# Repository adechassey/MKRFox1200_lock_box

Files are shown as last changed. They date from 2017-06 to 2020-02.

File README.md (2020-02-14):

# [MKRFox1200](http://www.sigfox.com/) Lock Box :key: 

<a href="https://www.buymeacoffee.com/antoine" target="_blank">Buy Me A Coffee</a>

What if you had to store something precious to be picked up by someone you do not know?
What if you were far away from the box and had to change the password for security reasons?

This is where Sigfox comes in! Indeed, Sigfox allows you to use 4 downlink messages per day. The idea is to be able to __update the password controlling the opening of the box__. Therefore in this tutorial, every 6 hours (4 times per day), the box's password will be set with a newly generated one from a web application. The owner can then decide to share the password to whom he wants. He will also __be notified every time the box is opened__!

<p align="center">
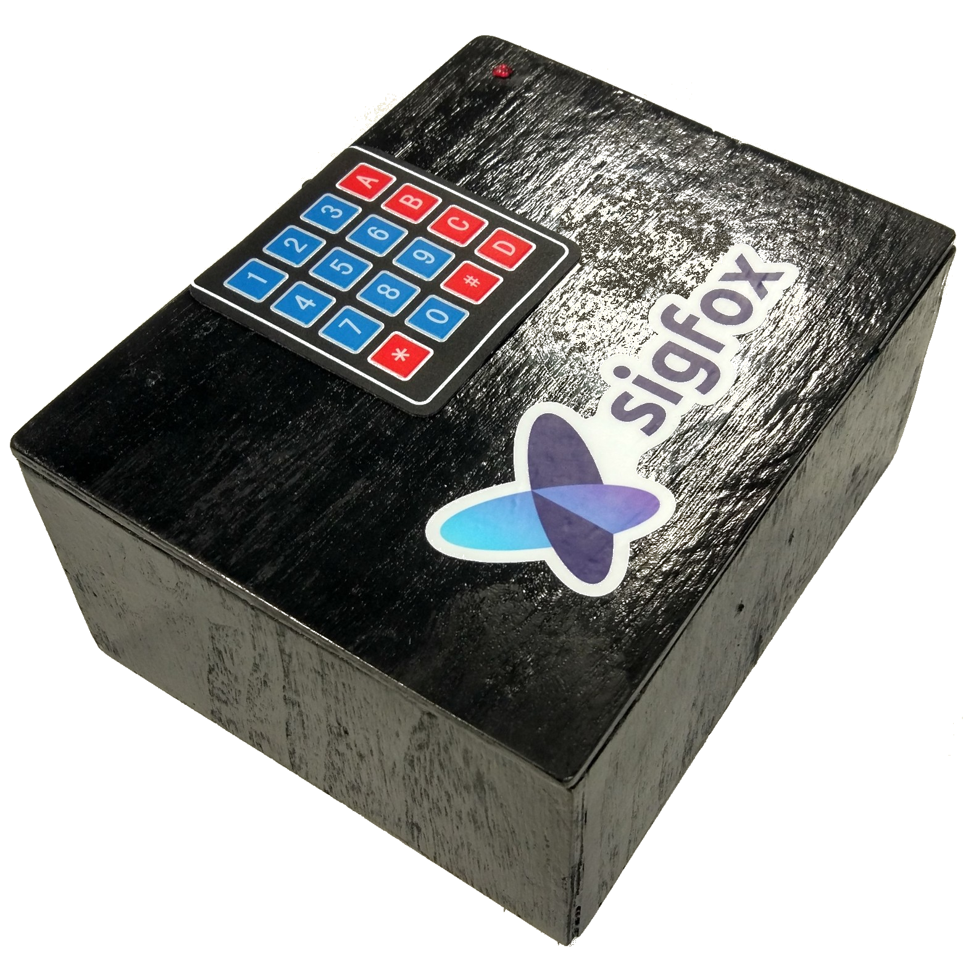
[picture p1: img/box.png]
    
</p>

This repository includes:
- the firmware to upload on the MKRFox1200
- the web API generating a new password and receiving the box's notifications

A video presentation is available [here](https://youtu.be/BI61gZuiOqs)!

Some photos showing how the mechanical part works:

:unlock: Opened state:
<p align="center">
    
</p>

:lock: Locked state:
<p align="center">
    
</p>

Making the box:
<p align="center">
    
</p>

Below is a diagram showing how the global system works:
    <p align="center">
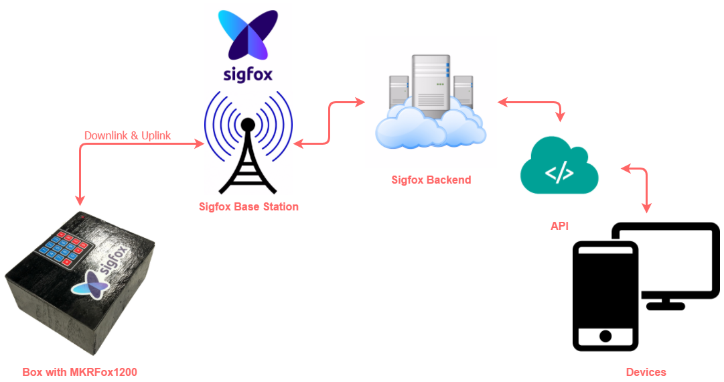
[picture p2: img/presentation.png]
        
    </p>

## Hardware Requirements

- an [MKRFox1200](https://www.arduino.cc/en/Main.ArduinoBoardMKRFox1200) board
- a [4x4 membrane keypad](http://www.ebay.com/itm/4-x-4-Matrix-Array-16-Key-Membrane-Switch-Keypad-Keyboard-for-Arduino-AVR-PI-C-/310511616357)
- a [buzzer](http://www.ebay.com/itm/DC-3-12V-110DB-Discontinuous-Beep-Alarm-Electronic-Buzzer-Sounder-LW-/172369764855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)
- an [RGB led](https://www.adafruit.com/product/159)
- a [servo motor](http://www.ebay.com/itm/9G-SG90-Micro-Servo-motor-RC-Robot-Helicopter-Airplane-Control-Car-Boat-/172420250871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)
- 2x AA batteries or equivalent (in this tutorial I use a [3.7 Li-Ion battery](https://www.adafruit.com/product/1781))
- some [jumper wires](https://www.adafruit.com/product/759) and a breadboard
- a box with a lock system

<p align="center">
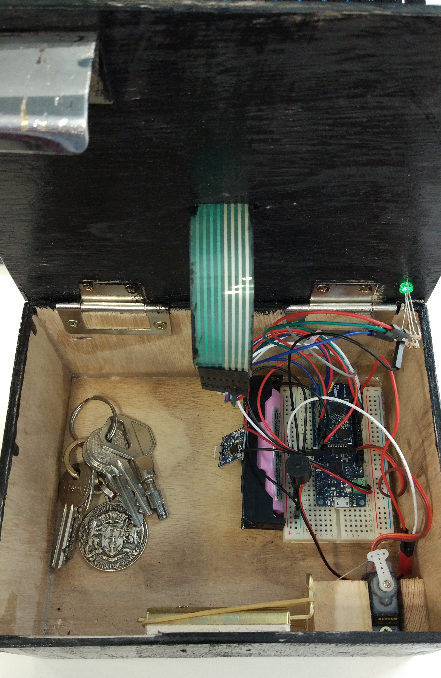
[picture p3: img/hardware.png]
    
</p>

## Installation
Start by cloning the repo: `git clone https://github.com/AntoinedeChassey/MKRFox1200_lock_box`

### MKRFox1200
1. [Activate](https://backend.sigfox.com/activate/arduino) your board on the Sigfox Backend _(you can follow __[this](https://www.arduino.cc/en/Guide/MKRFox1200)__ and  __[this](https://www.arduino.cc/en/Tutorial/SigFoxFirstConfiguration)__ tutorials)_
2. Flash the MKRFox1200 with the firmware located in this folder: _MKRFox1200_lock_box/MKRFox1200/__src___ (I used __[PlatformIO](http://platformio.org/)__ a new great IDE for IoT. After being installed on Atom, the folder "MKRFox1200" can be imported with `File>Open Folder...>Select` and the project will be configured automatically with the Arduino core and libraries - defined in the file `platformio.ini`)
3. Make sure to respect the correct __pin mapping__ (check `Defines & variables` in the code)

Some informations regarding the data frames being sent from the MKRFox1200 to the Sigfox Backend (_12 bytes maximum_):
- `getPasswordBySigfox()` sends the following:

| Byte | Type | Content |
| --- | --- | --- |
| 1 -> 6  | char  | "UPDATE"  |
| 7 -> 10  | float - Little Endian | Estimated battery voltage |

- `sendAlertBySigfox()` sends the following:

| Byte  | Type | Content |
| --- | --- | --- |
| 1 -> 4  | char  | "OPEN"
| 5 -> 8  | float - Little Endian | Estimated battery voltage |

You can help yourself with [this](http://www.scadacore.com/field-tools/programming-calculators/online-hex-converter/) website to decode hexadecimal (the battery voltage is a `Float - Little Endian (DCBA)`).

__FYI:__ the estimated battery voltage is only indicating a __very__ rough approximation. It is not a reliable piece of information at all but it will help you get an idea. A better approximation would be made with a 5V battery using the following formula: `float voltage = sensorValue * (5 / 1023)`

### Web Application

In this tutorial we will use ___Flask___ to build our little API. Flask is a microframework for Python which simplifies the creation of web applications. ___ngrok___ will be used to expose it through an online tunnel, this means it will be deployed on YOUR computer for simplicity purposes. Of course, you can decide to deploy it on a private server or PaaS (Platform as a Service) if you wish (this is not presented in this tutorial in order to keep it as short as possible).
> Please keep in mind Python with Flask can be substituted with any other kind of web application created with a totally different programming language! :wink:

1. Edit the "app.py" script (in folder _MKRFox1200_access_control/__API__/_)
2. Set the `deviceId` variable with your own MKRFox1200 device ID (you can find it when you actived your board or on the [Sigfox Backend](https://backend.sigfox.com/devicetype/list))
3. Install the Flask module with pip (Linux commands):
    ```bash
    $ sudo apt-get update && sudo apt-get -y upgrade
    $ sudo apt-get install python-pip3
    $ pip3 install flask
    ```
4. Launch the Python script _(on windows, if a PATH environment variable has not been created, the Python executable must be accessible from `C:\Users\USERNAME\AppData\Local\Programs\Python\Python36-32\python.exe`)_:

    ```bash
    $ cd MKRFox1200_access_control/API/
    $ python app.py
    ```

    If everything went fine, you must be able to access http://localhost:5000/ and see a result in your browser.
    There is an endpoint configured to generate a new password when calling http://localhost:5000/getPassword. This will also be used for the Sigfox Backend Callback configuration.

    Now we'll take a look at ngrok as a method of exposing your Python server publicly so that the Sigfox Backend can GET/POST data to it.
    This is particularly useful for testing purposes as we do not have to spend time on server configurations.
5. Install ngrok from __[here](https://ngrok.com/download)__
2. Launch ngrok on port 5000:
    ```bash
    $ ngrok http 5000
    ```
    This will expose your server publicly (on port 5000). To double check that this has worked, copy the address that has appeared in your terminal window under "forwarding" and navigate to it using your browser; it should look something like below. Make note of this as we'll need it below!

    <p align="center">
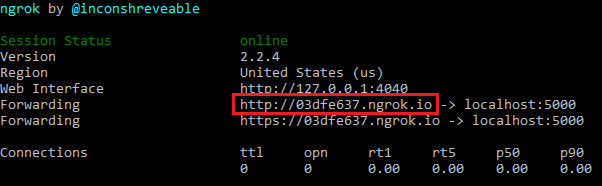
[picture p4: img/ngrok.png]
        
    </p>

### Sigfox Backend Callback
1. Log in __[here](https://backend.sigfox.com/auth/login)__
2. Go to <https://backend.sigfox.com/devicetype/list>, click left on your device row and select "Edit"
3. Under "Downlink data", select the `CALLBACK` "Downlink mode"

    <p align="center">
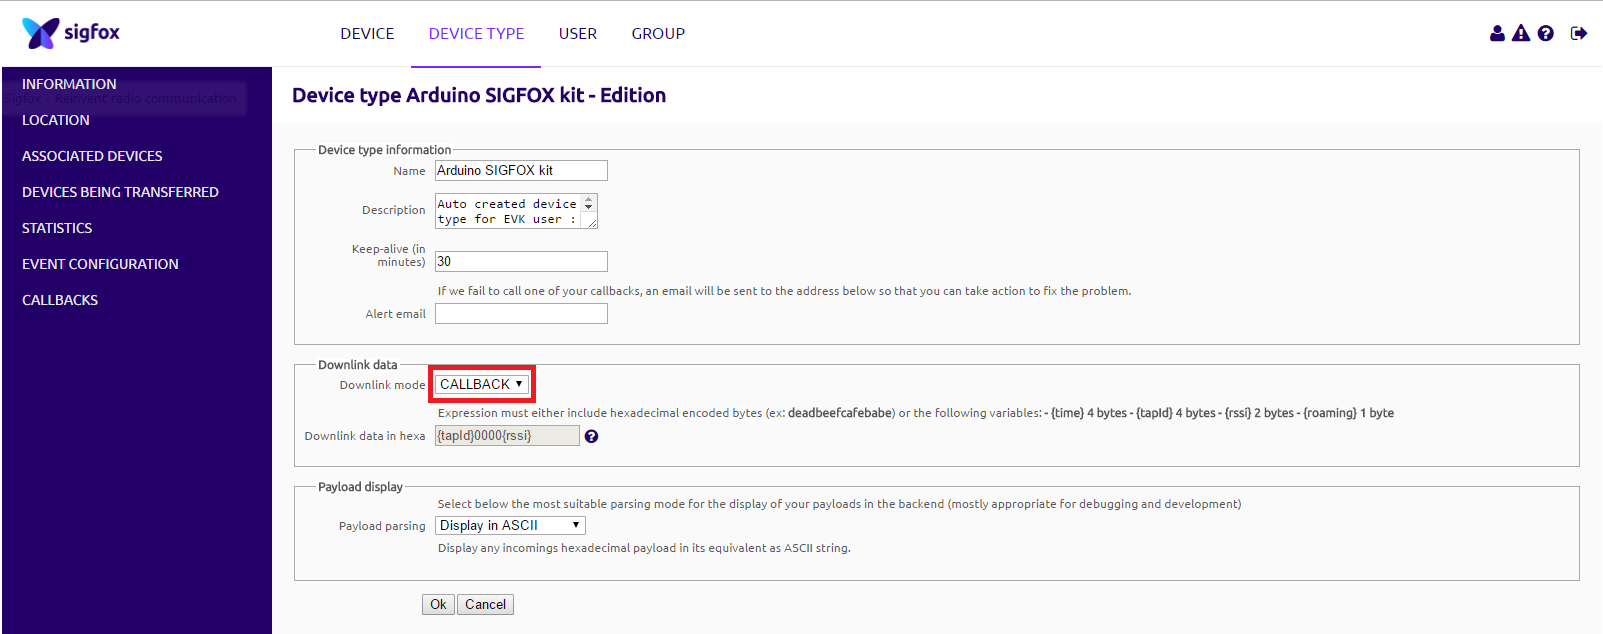
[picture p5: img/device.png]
        
    </p>

4. Now go to the "CALLBACKS" section on the left, select "new" on the top right, select "Custom Callback"
    * Type: `DATA` | `BIDIR`
    * Channel `URL`
    * Url pattern: `http://<YOUR_ngrok_SERVER_ADDRESS>/getPassword`
    * Use HTTP Method: `POST`
    * Content Type: `application/json`
    * Body: _(this will be sent to the API)_
    ```javascript
    {
          "device" : "{device}",
          "time" : "{time}",
          "duplicate" : "{duplicate}",
          "snr" : "{snr}",
          "rssi" : "{rssi}",
          "avgSnr" : "{avgSnr}",
          "station" : "{station}",
          "lat" : "{lat}",
          "lng" : "{lng}",
          "seqNumber" : "{seqNumber}",
          "data" : "{data}"
    }
    ```

5. Select "OK" to validate
6. __Tick__ the "Downlink" button to activate the newly created callback, make sure it looks like below

    <p align="center">
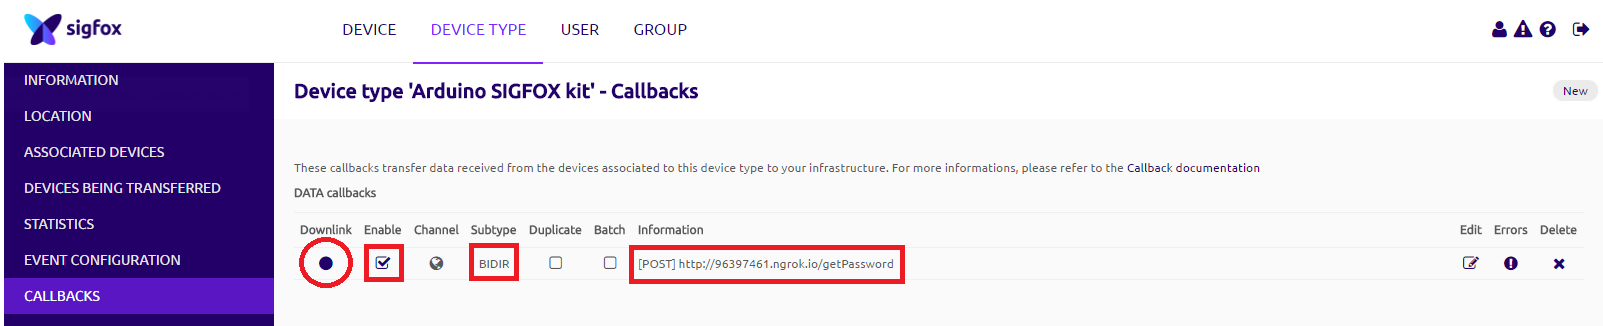
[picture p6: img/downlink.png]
        
    </p>

## Usage
- Power up the system
- The default password is `2017`
- The buffer storing the input (keys pressed) is 4 characters long
- This buffer is emptied every 3 seconds and the timer emptying it is paused every time there is a new key being pressed
- Press `*` to reset the input or __lock__ the box
- For debug purposes, you can press `#` to reset the password to its default (2017)
- A new generated password will be set every 6h by default, see: `const long interval = 1000 * 60 * 60 * 6` (this means a downlink will be asked every 6h = 4 per day to the [Sigfox](http://www.sigidwiki.com/wiki/SIGFOX) Backend, this respects the [ETSI](http://www.etsi.org/) Standards)
- The new password will be stored in the MKRFox1200 flash memory (this means that if you reboot the board, the default password (2017) is set again)
- The new password is accessible on the ngrok Python API (home page - http://localhost:5000/)
- Each time the correct password is entered, the message "OPEN" is sent to the Sigfox Backend so the owner can be notified it has been opened by someone (this takes 6 seconds)

## TODO - Going Further
- [x] send notification when the box is opened
- [x] send the approximated voltage of the 3.7V battery when there is a downlink (every 6h)
- [ ] add multi-tasking to allow asynchronous jobs
- [ ] put the board in deepsleep when not in use to preserve battery consumption

__Have fun__ and always keep your keys safe! :wink: :key:

> *Antoine de Chassey*

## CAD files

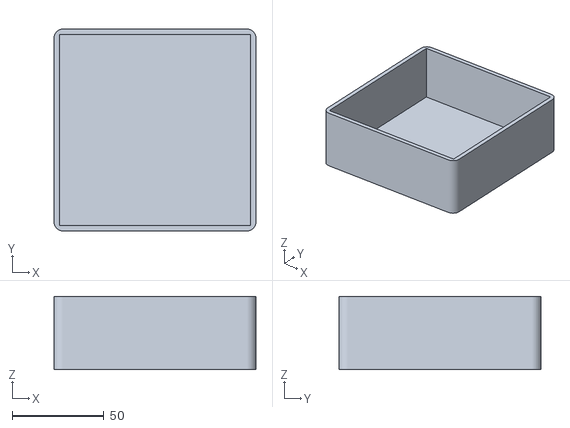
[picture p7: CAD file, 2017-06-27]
3D/Lock_box_bottom.stl
110.0 x 110.0 x 40.0

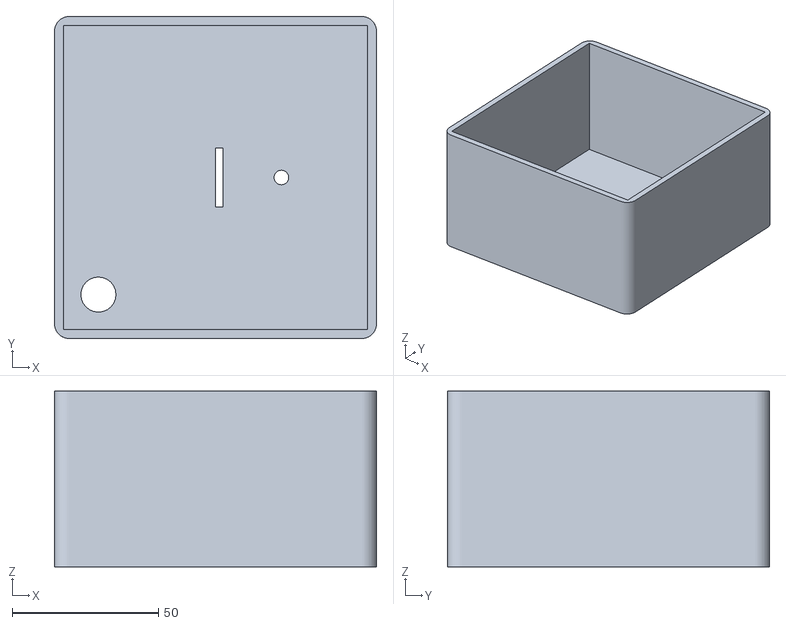
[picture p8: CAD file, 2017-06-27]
3D/Lock_box_top.stl
110.0 x 110.0 x 60.0

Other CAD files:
3D/Lock Box.skp

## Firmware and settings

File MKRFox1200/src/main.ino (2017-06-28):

// -------------------------------------------------------------------------------------
// This project controls and notifies access by updating rights with the Sigfox network
//
// Created: 16.06.2017
// Author: Antoine de Chassey
// Code: https://github.com/AntoinedeChassey/MKRFox1200_lock_box
// -------------------------------------------------------------------------------------

#include "SigFox.h"
#include "ArduinoLowPower.h"
#include "Keypad.h"
#include "Servo.h"
#include "SimpleTimer.h"

// Defines & variables
#define DEBUG true                // Set DEBUG to false to disable serial prints
// Pins
#define SERVO_PIN   5
#define BUZZER_PIN  4
#define RED_PIN     12
#define GREEN_PIN   11
#define BLUE_PIN    10

const byte ROWS = 4;  // Four rows
const byte COLS = 4;  // Four columns
// Define the cymbols on the buttons of the keypads
byte hexaKeys[ROWS][COLS] = {
        {'1','2','3','A'},
        {'4','5','6','B'},
        {'7','8','9','C'},
        {'*','0','#','D'}
};
byte rowPins[ROWS] = {0, 1, 2, 3};   // Connect to the row pinouts of the keypad
byte colPins[COLS] = {6, 7, 8, 9};   // Connect to the column pinouts of the keypad

char password[4]   = {'2', '0', '1', '7'};   // The default password byte array
char input[4]      = {};                     // The input byte array - 4 digits
int counter        = 0;                      // The counter used to fill the array
int timerId;
unsigned long previousMillis = 0;            // Will store last updated time
const long interval = 1000 * 60 * 60 * 6;    // Interval at which to ask for a new password (every 6 hours)

typedef union {
        float voltage;
        uint8_t bytes[4]; // Float - Little Endian (DCBA)
} FLOATUNION_t;

// Objects
// Initialize an instance of class NewKeypad
Keypad customKeypad = Keypad(makeKeymap(hexaKeys), rowPins, colPins, ROWS, COLS);
Servo myServo;
SimpleTimer timer;
RTCZero rtc;

void setup() {
        pinMode(BUZZER_PIN, OUTPUT);
        pinMode(RED_PIN, OUTPUT);
        pinMode(GREEN_PIN, OUTPUT);
        pinMode(BLUE_PIN, OUTPUT);

        if (DEBUG) {
                // We are using Serial1 instead than Serial because we are going in standby
                // and the USB port could get confused during wakeup. To read the DEBUG prints,
                // connect pins 13-14 (TX-RX) to a 3.3V USB-to-serial converter
                Serial1.begin(115200);
                while (!Serial1) {}
        }

        if (!SigFox.begin()) {
                // Something is really wrong, try rebooting
                // Reboot is useful if we are powering the board using an unreliable power source
                // (eg. solar panels or other energy harvesting methods)
                reboot();
        }

        // Send module to standby until we need to send a message
        SigFox.end();

        if (DEBUG) {
                // Enable DEBUG prints and LED indication if we are testing
                SigFox.debug();
        }

        timerId = timer.setInterval(3000, emptyInputBuffer); // Initialize the timer to executre the emptyInputBuffer function every X seconds

        lock(); // Make sure to lock the box
}

void loop() {
        unsigned long currentMillis = millis();
        if (currentMillis - previousMillis >= interval) {
                // save the last time you read the sensor
                previousMillis = currentMillis;
                updatePasswordBySigfox();
        }

        timer.run();
        char inputKey = customKeypad.getKey();

        if(inputKey) {
                switch (inputKey) {
                case '*':
                        lock();
                        blinkRedLED();
                        break;
                case '#':
                        password[0] = '2';
                        password[1] = '0';
                        password[2] = '1';
                        password[3] = '7';
                        tone(BUZZER_PIN, 5000, 50);
                        delay(100);
                        tone(BUZZER_PIN, 2000, 50);
                        delay(100);
                        tone(BUZZER_PIN, 2000, 50);
                        delay(100);
                        tone(BUZZER_PIN, 5000, 50);
                        break;
                default:
                        // Buzz the buzzer
                        tone(BUZZER_PIN, 1000, 100);
                        // Restart the timer
                        timer.restartTimer(timerId);
                        // Disable the timer because someone is typing
                        timer.disable(timerId);
                        if (counter == sizeof(input)) {
                                counter = 0;
                        }
                        input[counter] = inputKey;
                        counter++;

                        Serial.print(password);
                        Serial.print(" : ");
                        Serial.println(input);

                        if (passwordIsValid())
                                open();

                        if (counter == sizeof(input)) {
                                Serial.println("Waiting for new input...");
                                // Empty buffer
                                emptyInputBuffer();
                                blinkRedLED();
                        }
                        // Enable the timer back
                        timer.enable(timerId);
                }
        }
}

void setLEDColor(int red, int green, int blue) {
        analogWrite(RED_PIN, red);
        analogWrite(GREEN_PIN, green);
        analogWrite(BLUE_PIN, blue);
}

void blinkRedLED(){
        // BLink the LED in RED
        setLEDColor(0, 0, 0); // off
        delay(100);
        setLEDColor(255, 0, 0); // red
        delay(100);
        setLEDColor(0, 0, 0); // off
        delay(100);
        setLEDColor(255, 0, 0); // red
}

void reboot() {
        NVIC_SystemReset();
        while (1) ;
}

void emptyInputBuffer() {
        memset(input, 0, sizeof input);
        counter = 0;
        if(DEBUG) {
                Serial.print(password);
                Serial.print(" : ");
                Serial.println(input);
        }
}

bool passwordIsValid() {
        for(u_int i=0; i<sizeof(input); i++) {
                if(password[i] != input[i]) {
                        return false;
                }
        }
        return true;
}

void open() {
        myServo.attach(SERVO_PIN);
        digitalWrite(SERVO_PIN, HIGH);
        myServo.write(110);
        delay(500);
        digitalWrite(SERVO_PIN, LOW);
        myServo.detach(); // detach servo to stop it working
        emptyInputBuffer();
        setLEDColor(0, 255, 0); // green
        sendAlertBySigfox();
}

void lock() {
        // Buzz the buzzer
        tone(BUZZER_PIN, 5000, 50);
        delay(100);
        tone(BUZZER_PIN, 5000, 50);
        myServo.attach(SERVO_PIN);
        digitalWrite(SERVO_PIN, HIGH);
        myServo.write(35);
        delay(500);
        digitalWrite(SERVO_PIN, LOW);
        myServo.detach(); // detach servo to stop it working
        emptyInputBuffer();
        setLEDColor(255, 0, 0);  // red
}

void updatePasswordBySigfox() {
        Serial.println("Fetching new password with Sigfox!");

        // Build the frame to be sent
        uint8_t msg[10];
        msg[0] = 'U';
        msg[1] = 'P';
        msg[2] = 'D';
        msg[3] = 'A';
        msg[4] = 'T';
        msg[5] = 'E';
        FLOATUNION_t voltage = getEstimatedBatteryVoltage();
        msg[6] = voltage.bytes[0];
        msg[7] = voltage.bytes[1];
        msg[8] = voltage.bytes[2];
        msg[9] = voltage.bytes[3];

        // Disable the timer
        timer.disable(timerId);
        // Set the LED to blue
        setLEDColor(0, 0, 255);

        // Start the module
        SigFox.begin();
        // Wait at least 30mS after first configuration (100mS before)
        delay(100);
        // Clears all pending interrupts
        SigFox.status();
        delay(1);

        SigFox.beginPacket();
        SigFox.write(msg, sizeof(msg));

        int ret = SigFox.endPacket(true); // send buffer to SIGFOX network and wait for a response
        if(ret > 0) {
                Serial.println("No transmission");
        } else {
                Serial.println("Transmission ok");
        }

        Serial.println(SigFox.status(SIGFOX));
        Serial.println(SigFox.status(ATMEL));

        if(SigFox.parsePacket()) {
                Serial.println("Response from server:");
                int counter = 0;
                while(SigFox.available()) {
                        // Serial.print("0x");
                        // Serial.println((char) SigFox.read(), HEX);
                        char incomingChar = char(SigFox.read());
                        if(counter < 4 && incomingChar != ' ') {
                                Serial.println(incomingChar);
                                password[counter] = incomingChar;
                        } else {
                                SigFox.read();
                        }
                        counter++;
                }
        } else {
                Serial.println("Could not get any response from the server");
                Serial.println("Check the SigFox coverage in your area");
                Serial.println("If you are indoor, check the 20dB coverage or move near a window");
        }
        Serial.println();

        SigFox.end();

        // Make sure the box is locked with the new password
        lock();
        // Enable the timer back
        timer.enable(timerId);
}

void sendAlertBySigfox() {
        Serial.println("Sending alert by Sigfox!");

        // Build the frame to be sent
        uint8_t msg[8];
        msg[0] = 'O';
        msg[1] = 'P';
        msg[2] = 'E';
        msg[3] = 'N';
        FLOATUNION_t voltage = getEstimatedBatteryVoltage();
        msg[4] = voltage.bytes[0];
        msg[5] = voltage.bytes[1];
        msg[6] = voltage.bytes[2];
        msg[7] = voltage.bytes[3];

        // Disable the timer
        timer.disable(timerId);

        // Start the module
        SigFox.begin();
        // Wait at least 30mS after first configuration (100mS before)
        delay(100);
        // Clears all pending interrupts
        SigFox.status();
        delay(1);

        SigFox.beginPacket();
        SigFox.write(msg, sizeof(msg));

        int ret = SigFox.endPacket();
        if(ret > 0) {
                Serial.println("No transmission");
        } else {
                Serial.println("Transmission ok");
        }

        Serial.println(SigFox.status(SIGFOX));
        Serial.println(SigFox.status(ATMEL));
        SigFox.end();

        // Lock the box automatically after sending notification
        lock();
        // Enable the timer back
        timer.enable(timerId);
}

FLOATUNION_t getEstimatedBatteryVoltage() {
        FLOATUNION_t battery;
        // Read the input on analog pin 0:
        int sensorValue = analogRead(ADC_BATTERY);
        // Convert the analog reading (which goes from 0 to ~757.02 at 3.7V) if you use a 5V battery the formula becomes: sensorValue * (5 / 1023)
        float voltage = sensorValue * (3.7 / 400);
        battery.voltage = voltage;
        if (DEBUG) {
                Serial.println("Battery estimation hexadecimal 4 bytes float:");
                for (u_int i=0; i<sizeof(battery.bytes); i++)
                {
                        Serial.print(battery.bytes[i], HEX); // Print the hex representation of the float
                        Serial.print(' ');
                }
                Serial.println("Voltage: " + String(battery.voltage) + "V");
        }

        return battery;
}

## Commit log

2017-06-16 Updated timers and functions
2017-06-27 Added img and 3D Updated README.md Added multi-tasking
    [Lock Box.skp, Lock_box_bottom.stl, Lock_box_top.stl]
2017-06-28 Added more complex frames
